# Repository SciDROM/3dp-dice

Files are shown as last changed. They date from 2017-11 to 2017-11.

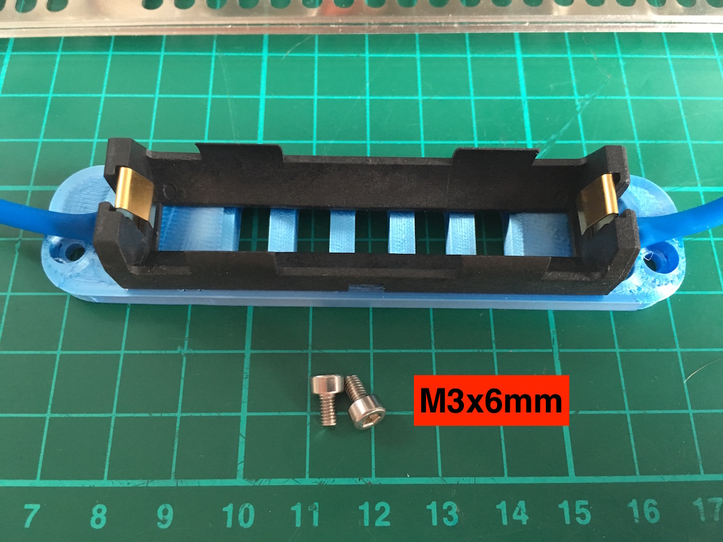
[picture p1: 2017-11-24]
optional/PiUSV+/parts.jpg

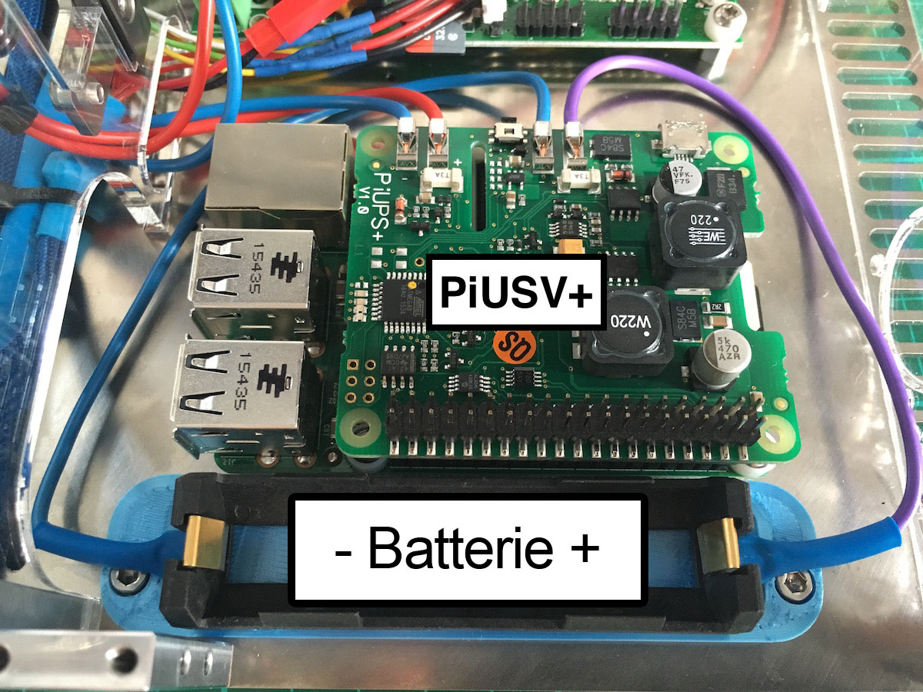
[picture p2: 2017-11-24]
optional/PiUSV+/whole_assembly.jpg

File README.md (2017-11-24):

# 3dp-dice

From https://well-engineered.net/index.php/en/projects/35-build-your-own-dice

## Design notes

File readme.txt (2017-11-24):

========================================

========================================

GERMAN:

30. April 2016 - Der Inhalt wird derzeit noch erstellt und komplettiert. Bei Fertigstellung wird dieses Dokument angepasst.

========

In diesem Ordner befinden sich alle benötigten Quelldateien für den Bau des 3D-Druckers „DICE“.

Die Benutzung ist unter folgenden Bedingungen erlaubt: Namensnennung - Nicht-kommerziell - Weitergabe unter gleichen Bedingungen 
CC BY-NC-SA

Diese Lizenz erlaubt es anderen, das Werk zu verbreiten, zu remixen, zu verbessern und darauf aufzubauen, allerdings nur nicht-kommerziell und solange René Jurack als Urheber des Originals genannt wird und die auf seinem Werk basierenden neuen Werke unter denselben Bedingungen veröffentlicht werden.

Link zur BOM (bill of material): https://docs.google.com/spreadsheets/d/1rdxKzCCWACPqPtby6bYP5xPDgSupsl8gtncckqbfDJk/

========================================

========================================

ENGLISH:

30. April 2016 - Files are under construction and needed to make complete. If finished, this document is going to get updated.

========

In this folder are all needed files to build the „DICE“.

Use it under following license: CC BY-NC-SA

Link to BOM (bill of material): https://docs.google.com/spreadsheets/d/1rdxKzCCWACPqPtby6bYP5xPDgSupsl8gtncckqbfDJk/

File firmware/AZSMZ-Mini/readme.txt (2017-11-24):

Config:

As of 15th may 2016: config.txt verified.

Firmware is Smoothieware.

Provided config-file is for the AZSMZ-mini V2.1 and to use in the 3D-printer ‚DICE’. More information at www.well-engineered.net

Firmware:

- always-up-to-date smoothieware-firmware to get at (deep-link): https://github.com/Smoothieware/Smoothieware/tree/edge/FirmwareBin

- Firmware.bin in this dropbox-folder is from 10. May 2016 (in case you are lazy and don’t want to download the newest)

How to:

- download firmware.bin from link above and save on SD-card

- save config.txt from dropbox on SD-card, too

- put SD-card into AZSMZ-mini, power on and press the reset-button once.

- wait for firmware to get ready.

- done.

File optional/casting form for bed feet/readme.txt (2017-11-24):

Cast for casting the distance sleeves beneath the printed.

Castmaterial is silicon for molds. (preferred).

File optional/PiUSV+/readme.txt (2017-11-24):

Battery mount for battery holder.
Battery is used for PiUSV+

Holder: https://www.reichelt.de/Batteriehalter-fuer-sonstige-Zellen/HA-1X18650-SA/3/index.html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

Battery: https://www.reichelt.de/Industriezellen/SANYO-18650-PCB/3/index.html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

PiUSV+: https://www.reichelt.de/Weiteres-Zubehoer/RPI-USV-/3/index.html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

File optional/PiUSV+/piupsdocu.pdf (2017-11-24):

CW2. PiUSV+

# CW2. PiUPS+

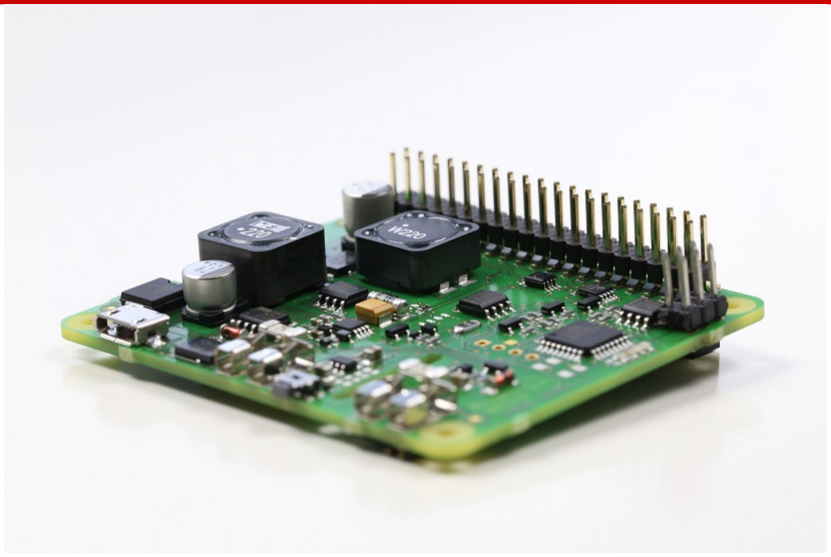
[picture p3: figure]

## Documentation CW2. PiUPS+

# Contents

I Introduction | 4
1 Function | 5
2 Technical information | 6
II Installation | 8
3 Hardware | 9
4 Software | 13

# List of Figures

2.1 Connecting assignment PiUPS+ | | 6
3.1 Start jumper configuration manually | | 9
3.2 Start jumper configuration automatically | | 9
3.3 Connecting the rechargeable battery | | 10
3.4 PiUPS+ on the Raspberry Pi with rechargeable battery | | 11
3.5 PiUPS+ with adapter | | 11
3.6 Alternative primary input | | 12

# Part I

# Introduction

# 1 Function

The PiUPS+ is an extension board for the Raspberry Pi. This extension can be used to ensure that the Pi is shut down in a safe manner in event of power failure. Corrupt and defective file systems on the SD card are therefor a thing of the past with this. In order to monitor the status of the PiUPS+ and be able to control it, the PiUPS-Monitorïs available that must be installed on the operating system of the Pi.

- Shutting down the Raspberry Pi in a safe manner
- Bridging longer power failures
- Switching off the Pi’s manually via the button on the PiUPS+

# 2 Technical information

Input primary voltage USB | +5VDC MicroUSB
Input primary voltage alternative | +5VDC bis +25VDC
Output current | up to 2,000mA¹
Output voltage | +5VDC +- 0.2V
Communication | I²C via address 0x30
Dimensions | L x W x H: 65 mm x 56.5 mm x 20 mm (corresponds with Raspberry Pi HAT specification)

## 2.1 CONNECTING DIAGRAM

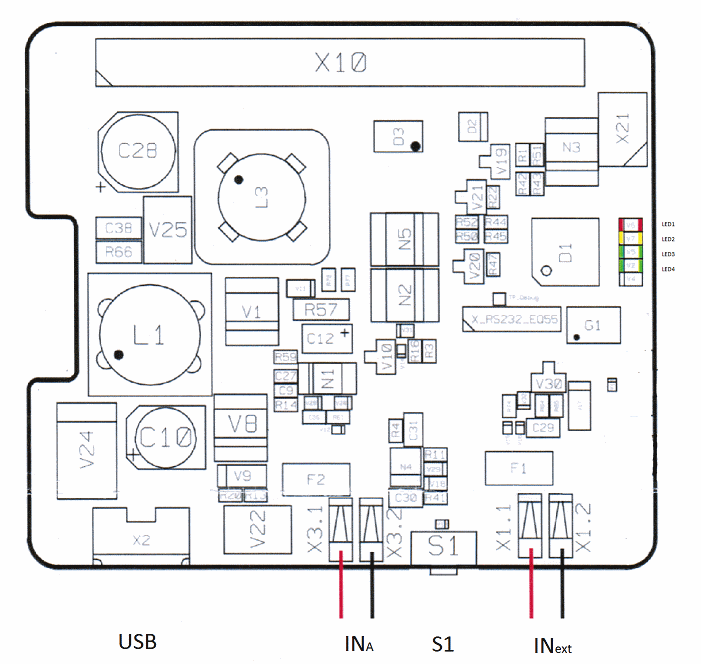
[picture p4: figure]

FIGURE 2.1: Connecting assignment PiUPS+

1depending on the power supply or rechargeable battery used

USB | MicroUSB-Buchse
INa | Connection of the rechargeable batteries (red = +, black = -)
INext | Alternative primary input. Permissible voltage +5VDC to +25VDC (red = +, black = -)
S1 | Switch for switching on / off (configuration via jumpers on the bottom)
LED1 (red) | LED illuminates: operation via both rechargeable battery, LED flashes: rechargeable battery not connected or is defective
LED2 (yellow) | Status display of the rechargeable battery. LED flashes: rechargeable battery charging, LED illuminates continuously: rechargeable battery charged
LED3 (green) | Status display PiUPS+. LED flashes: UPS operates correctly
LED4 (green) | Operation of the primary input

## 2.2 RECHARGEABLE BATTERY

The PiUPS+ can charge rechargeable batteries with the following specifications using the connection of the INa (Figure 2.1).Other rechargeable batteries / batteries must not be used under any circumstances.²

Technology | Lithium Ion (Li-Ion) or Lithium Polymer (LiPo)
Cells | 1
Capacity | min. 300mAh
Voltage | +3.7V
Discharge current | min. 3A
Charge voltage | +4.2V
Charge current | 100mA

2CW2. accepts no liability for damage caused by using other rechargeable batteries / batteries.

# Part II

# Installation

# 3 Hardware

Before commissioning the PiUPS+, you have to connect the rechargeable battery and configure the button as desired. We shall describe the precise process to you in the following steps.

## 3.1 SETTING THE BUTTON

The behaviour of the button of the PiUPS+ can be set using a jumper on the bottom of the PiUPS+. If you want to start the Pi manually via the button, you must insert the jumper in such a manner that it bridges both contacts.

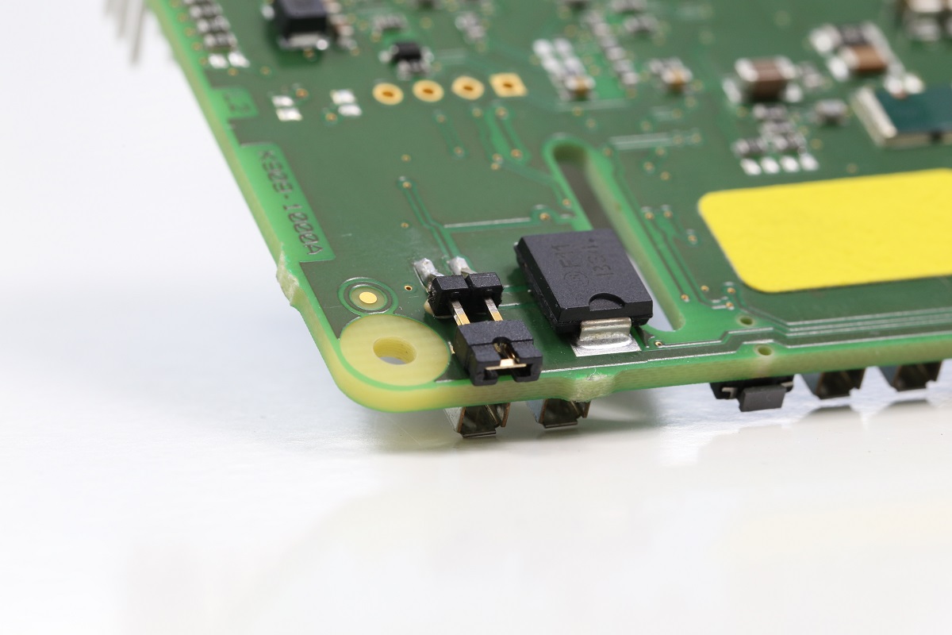
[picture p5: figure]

FIGURE 3.1: Start jumper configuration manually

If the Pi should be started automatically as soon as voltage is available at one of the primary inputs, insert the jumper so that the contacts are not connected.

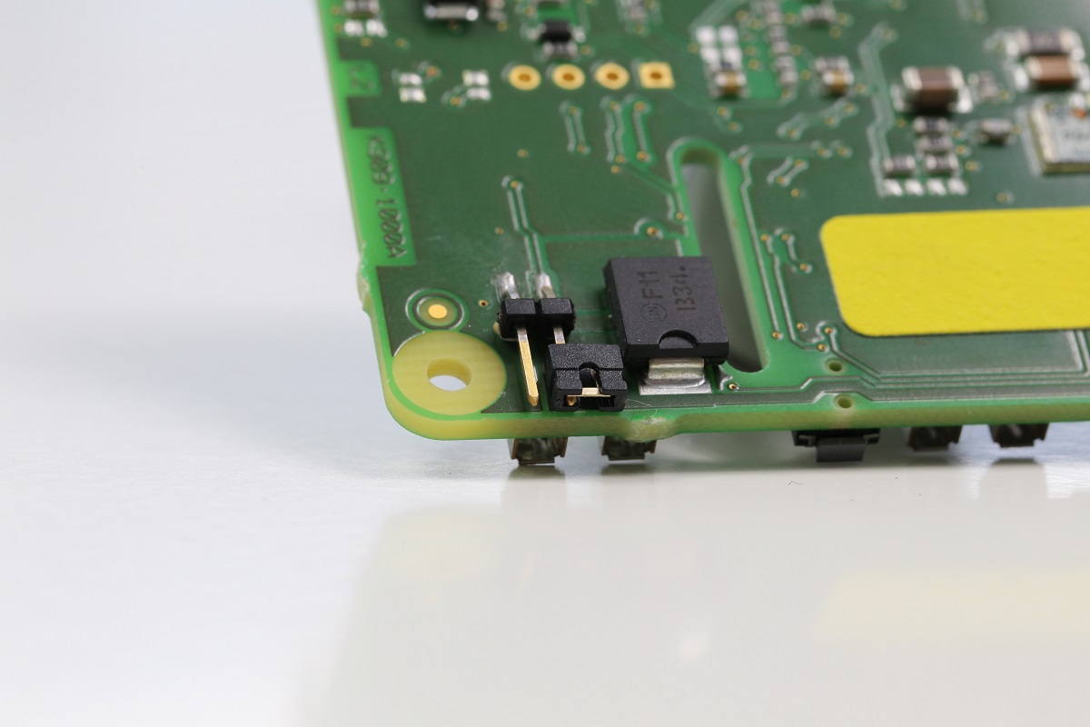
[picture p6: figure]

FIGURE 3.2: Start jumper configuration automatically

## 3.2 CONNECTING THE RECHARGEABLE BATTERY

ATTENTION! Please only use rechargeable batteries on this connection that have the specifications mentioned above. Other rechargeable batteries or batteries may lead to damaging the UPS and the Raspberry Pi!

Before you mount the PiUPS+ on the Pi, we recommend that you connect the rechargeable battery to the PiUPS+. In doing so, take care not to reverse the poles of the contacts for the rechargeable battery.
Generally, the rechargeable battery has a red braid and a black braid. Now please connect the connections of the rechargeable battery to the PiSUV+ as shown in the following figure.

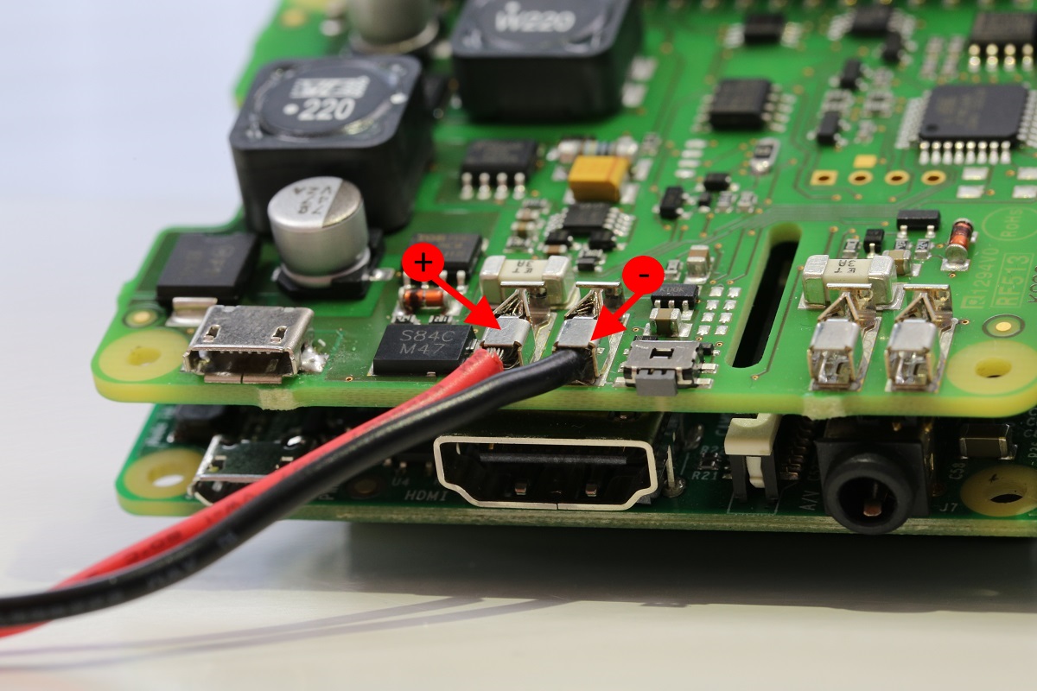
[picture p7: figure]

FIGURE 3.3: Connecting the rechargeable battery

## 3.3 INSTALLATION OF THE PIUPS+ ONTO THE RASPBER-

## RYPI

Now you can attach the PiUPS+ onto the RaspberryPi. Please note that in doing so, the pins of the GPIO ports cannot be inserted offset and the UPS cannot be attached to the Raspberry the wrong way around. This could lead to the destruction of the Pis and the PiUPS+.

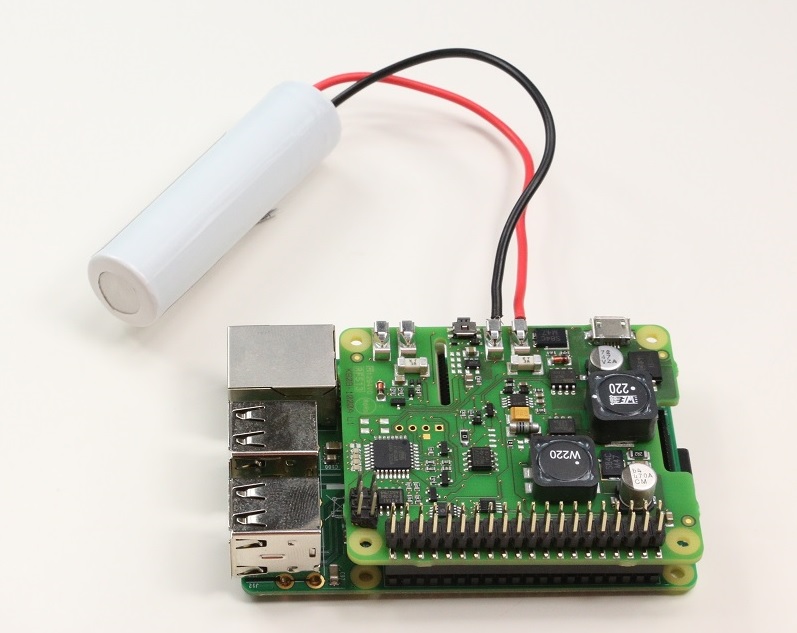
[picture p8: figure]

FIGURE 3.4: PiUPS+ on the Raspberry Pi with rechargeable battery

### 3.3.1 RASPBERRY PI MODEL A AND B

In order to be able to use the PiUPS+ wit Raspberry Pi model A or B, you need an adapter. Attach the adapter to the GPIO port of the Raspberry and ten the hPiUPS+ to the adapter as you can see in figure 3.5.

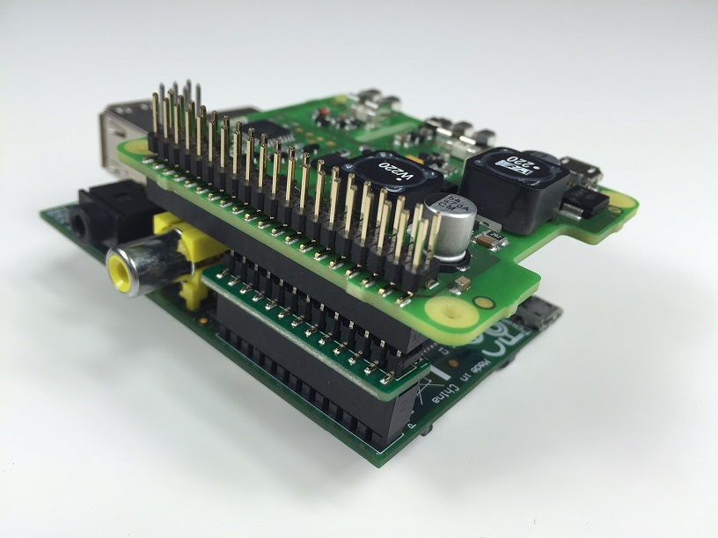
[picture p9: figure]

FIGURE 3.5: PiUPS+ with adapter

## 3.4 CONNECTING THE PRIMARY VOLTAGE

In order to be able to start the system, now you have to connect the primary voltage to the PiUPS+. Please do not use any USB power pack or active USB hubs on the Raspberry Pi. These may influence the function of the PiUPS+ so that switching off the system in a safe manner in event of power failure is not guaranteed.

### 3.4.1 USB

You can use the USB port on the PiUPS+ to supply the system with voltage. Depending on the configuration of the button, the system starts automatically or after you have pressed the button.

### 3.4.2 ALTERNATIVE INPUT

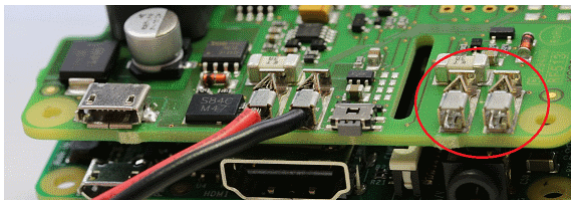
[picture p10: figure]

FIGURE 3.6: Alternative primary input

You can connect a voltage source with +5V to +25V to the alternative input. Please take note of the correct polarity when connecting (Figure 2.1)! These voltage sources are used instead of the USB port. The input is also monitored in the same manner as the USB port and in event of a power failure, the PiUPS+ automatically switches to the rechargeable battery connected in all cases.

# 4 Software

## 4.1 CONFIGURATION

You can influence the behaviour of the PiUPS monitor via the configuration. You have the following parameters at your disposal:

ShutdownTimer=<Time in seconds>
This value specifies how long the system continues to run after the voltage supply has switched to the rechargeable battery. Values between 1 - 999.999.999. are possible.

PowerOffTimer=<Time in seconds>
This value specifies how long the PiUPS+ should still stay switched on after the commend to shut down has been sent. A value between 1 - 255 can be entered here.

ShutdownCmd=<Command line>
This option is used to specify a command that should be used to shut down the Pi-UPS+. Here, e.g., you can enter the command for switching off or store your own script . If you store your own script, take care that the operating system is shut down by the script.

LogLevel=<notice|error|debug>
With this option, you can control which entries should be stored in the log.

LogStatusDesc=<0|1>
This command is used to influence if only a numeric value is logged for this value when changing the status, or a description as well.

## 4.2 RASPBIAN

Please download the current version of the des PiUPS monitor for the PiUPS+ from the support screen:
http://piups.net/support/

### 4.2.1 PREPARING FOR INSTALLATION

In order to allow the PiUPS monitor to operate correctly, the I²C-Bus must be activated first. Good instructions can be found the following screen: https://learn.adafruit.com/adafruits-raspberry-pi-lesson-4-gpio-setup/configuring-i2c

### 4.2.2 INSTALLATION

In order to be able to install the package under Raspbian, you must execute the following command in the directory with the package downloaded.

1 | sudo dpgk - i piupsmon - 0 . 8 . deb

### 4.2.3 USEAGE

When the PiUPS monitor is installed, you have the following commands available for starting and stopping the monitor:

1 | sudo / etc / i n i t . d/piupsmon s t a r t
1 | sudo / etc / i n i t . d/piupsmon stop
1 | sudo / etc / i n i t . d/piupsmon s ta t u s
| You can adapt the configuration in the following file: /etc/piupsmon/piupsmon.conf Do not forget to restart the PiUPS monitor after making an adjustment!
| The PiUPS monitor also saves a log in the following file: /var/log/piupsmon.log

## 4.3 MORE DISTRIBUTIONS

| We will be releasing packages for further distributions within the next few weeks. We shall also make the source text of the PiUPS monitor available online within the next few days.

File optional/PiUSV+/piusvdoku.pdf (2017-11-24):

CW2. PiUSV+

# CW2. PiUSV+


## Dokumentation CW2. PiUSV+

# Inhaltsverzeichnis

I Einführung | 4
1 Funktion | 5
2 Technische Informationen | 6
II Installation | 8
3 Hardware | 9
4 Software | 13

# Abbildungsverzeichnis

2.1 Anschlussbelegung PiUSV+ | | 6
3.1 Jumperkonfiguration manueller Start | | 9
3.2 Jumperkonfiguration automatischer Start | | 9
3.3 Anschluss Akku | | 10
3.4 PiUSV+ auf Raspberry Pi mit Akku | | 11
3.5 PiUSV+ mit Adapter | | 11
3.6 Alternativer Primäreingang | | 12

# Teil I

# Einführung

# 1 Funktion

Die PiUSV+ ist eine Erweiterungsplatine für den Rapberry Pi. Mit dieser Erweiterung können Sie sicherstellen, dass der Pi im Falle eines Stromausfalles sicher heruntergefahren wird. Korrupte und defekte Dateisysteme auf der SD-Karte gehören damit der Vergangenheit an. Um den Status der PiUSV+ überwachen und zu steuern zu können, gibt es den ”PiUSV-Monitor”, der auf dem Betriebssystem des Pi installiert werden muss.

- Sicheres Herunterfahren des Raspberry Pi
- Überbrückung von längeren Stromausfällen
- Manuelles Ausschalten des Pi’s über Taster an PiUSV+

# 2 Technische Informationen

Eingang Primärspannung USB | +5VDC MikroUSB
Eingang Primärspannung Alternativ | +5VDC bis +25VDC
Ausgangsstrom | bis zu 2000mA¹
Ausgangsspannung | +5VDC +- 0.2V
Kommunikation | per I²C über Adresse 0x30
Abmessungen | L x B H: 65 mm x 56,5 mm x 20 mm (entspricht Raspberry Pi HAT Vorgaben)

## 2.1 ANSCHLUSSPLAN


Abbildung 2.1: Anschlussbelegung PiUSV+

1Abhängig vom verwendeten Netzteil und Akku

USB | MikroUSB-Buchse
INa | Anschluss des Akkus (rot = +, schawarz = -)
INext | Alternativer Primäreingang. Zulässige Spannung +5VDC bis +25VDC (rot = +, schwarz = -)
S1 | Schalter zum Ein-/Ausschalten (Konfiguration über Jumper auf Unterseite)
LED1 (Rot) | Betrieb über Akku
LED2 (Gelb) | Status Anzeige des Akkus. LED Blinkt: Akku wird geladen, LED leuchtet dauerhaft: Akku ist voll
LED3 (Grün) | Status Anzeige PiUSV+. LED Blinkt: USV funktioniert ordnungsgemäß
LED4 (Grün) | Betrieb über Primäreingang

## 2.2 AKKU

Die PiUSV+ kann Akkus mit den folgenden Spezifikationen am Anschluss INa (Abbildung
2.1) aufladen. Es dürfen auf keinen Fall andere Akkus/Batterien verwendet werden.²
Technologie | Lithium Ionen (LiIon) oder Lithium Polymer (LiPo)
Zellen | 1
Kapazität | min. 300mAh
Spannung | +3.7V
Entladestrom | min. 3A
Ladespannung | +4.2V
Ladestrom | 100mA

2Für Schäden die durch die Verwendung von anderen Akkus oder Batterien entstehen übernimmt CW2.

keinerlei Haftung.

# Teil II

# Installation

# 3 Hardware

Vor der Inbetriebnahme der PiUSV+ müssen Sie den Akku anschließen und den Taster wie gewünscht konfigurieren. Den genauen Ablauf werden wir Ihnen in den nächsten Schritten erklären.

## 3.1 EINSTELLUNG TASTER

Das Verhalten des Tasters der PiUSV+ können Sie mit einem Jumper auf der Unterseite der PiUSV+ einstellen. Wenn Sie den Pi über den Taster manuell starten wollen, müssen Sie den Jumper so aufstecken, dass dieser die beiden Kontakte überbrückt.


Abbildung 3.1: Jumperkonfiguration manueller Start

Soll der Pi automatisch starten sobald die Spannung an einem der primären Eingänge anliegt, stecken Sie den Jumper so auf, dass die Kontakte nicht verbunden sind.


Abbildung 3.2: Jumperkonfiguration automatischer Start

## 3.2 ANSCHLUSS AKKU

ACHTUNG! Bitte verwenden Sie an diesem Anschluss nur Akkus mit den oben genannten Spezifikationen! Andere Akkus oder Batterien können zur Beschädigung der USV und des Raspberry Pi führen!

Bevor sie die PiUSV+ auf dem Pi montieren, empfehlen wir Ihnen den Akku an der PiUSV+ anzuschließen. Es ist dabei unbedingt darauf zu achten, dass die Kontakte des Akkus nicht verpolt werden.
In der Regel haben Sie am Akku eine rote Litze und eine schwarze Litze. Die Anschlüsse des Akkus schließen Sie nun bitte wie auf der folgenden Grafik gezeigt an der PiUSV+ an.


Abbildung 3.3: Anschluss Akku

## 3.3 INSTALLATION DER PIUSV+ AUF DEM RASPBERRYPI

Die PiUSV+ können Sie nun auf derm RaspberryPi aufstecken. Bitte beachten Sie dabei, dass die Pins der GPIO-Ports nicht versetzt gesteckt werden und die USV nicht verkehrtherum auf dem Raspberry aufgesetzt wird. Dies kann zur Zerstörung der Pis und der PiUSV+ führen.


Abbildung 3.4: PiUSV+ auf Raspberry Pi mit Akku

### 3.3.1 RASPBERRY PI MODELL A UND B

Um die PiUSV+ mit dem Raspberry Pi Modell A oder B verwenden zu können, benötigen Sie einen Adapter. Den Adapter stecken Sie auf die GPIO-Ports des Raspberry und die PiUSV+ anschließend auf den Adapter wie in Abbildung 3.5 zu erkennen.


Abbildung 3.5: PiUSV+ mit Adapter

## 3.4 ANSCHLUSS PRIMÄRSPANNUNG

Um das System nun starten zu können, müssen Sie noch die Primärspannung an der Pi-USV+ anschließen. Bitte verwenden Sie am Raspberry Pi kein USB-Netzteil, oder aktive USB Hubs. Diese können die Funktion der PiUSV+ beeinträchtigen, so dass kein sicheres Ausschalten des Systems bei einem Strommausfall gewährleistet ist.

### 3.4.1 USB

Sie können den USB-Eingang auf der PiUSV+ verwenden, um das System mit Spannung zu versorgen. Je nach Konfiguration des Tasters startet das System nun automatisch oder nachdem Sie auf den Schalter gedrückt haben.

### 3.4.2 ALTERNATIVER EINGANG


Abbildung 3.6: Alternativer Primäreingang

Am alternativen Eingang können Sie eine Spannungsquelle mit +5V bis +25V anschließen. Bitte achten Sie auf die korrekte Polung beim Anschließen (Abbildung 2.1)! Diese Spannungsquelle wird anstelle des USB-Eingangs verwendet. Der Eingang wird ebenfalls wie der USB-Eingang überwacht und die PiUSV+ schaltet im Falle des Stromausfalls automatisch auf den angeschlossenen Akku.

# 4 Software

## 4.1 KONFIGURATION

Sie können das Verhalten der PiUSV-Monitors über die Konfiguration beeinflussen. Ihnen stehen dazu folgende Parameter zur Verfügung:

ShutdownTimer=<Zeit in Sekunden>
Dieser Wert gibt an, wie lange das System weiter läuft, nachdem die Spannungsversorgung auf den Akku gewechselt ist. Es sind Werte zwischen 1 - 999.999.999. möglich.

PowerOffTimer=<Zeit in Sekunden>
Dieser Wert gibt an, wie lange die PiUSV+ noch eingeschaltet bleiben soll, nachdem der Befehl zum Herunterfahren gesendet wurde. Es kann hier ein Wert zwischen 1 -255 angegeben werden.

ShutdownCmd=<Befehlszeile>
Mit dieser Option geben Sie einen Befehl an, mit dem die PiUSV+ heruntergefahren werden soll. Sie können hier z.B. direkt den Befehl zum Ausschalten geben oder ein eigenes Skript hinterlegen. Wenn Sie ein eigenes Skript hinterlegen, müssen Sie darauf achten, dass das Betriebssystem durch das Skript heruntergefahren wird.

LogLevel=<notice|error|debug>
Mit dieser Option können Sie steuern, welche Einträge im Log gespeichert werden sollen.

LogStatusDesc=<0|1>
Mit dem Befehl können Sie beinflussen, ob bei Statusänderungen nur ein nummerischer Wert oder auch eine Beschreibung zu diesem Wert geloggt wird.

## 4.2 RASPBIAN

Bitte laden Sie sich die aktuellste Version des PiUSV-Monitors für die PiUSV+ auf der Support-Seite herunter:
http://piusv.de/support/

### 4.2.1 VORBEREITUNG INSTALLATION

Damit der PiUSV-Monitor ordnungsgemäß funktioniert, müssen Sie zuerst den I²C-Bus aktivieren.
Eine gute Anleitung dazu finden Sie auf der folgenden Seite: https://learn.adafruit.com/adafruits-raspberry-pi-lesson-4-gpio-setup/configuring-i2c

### 4.2.2 INSTALLATION

Um das Paket unter Raspbian zu installieren, müssen Sie folgenden Befehl im Verzeichnis mit dem heruntergeladenen Paket ausführen:

1 | sudo dpgk - i piupsmon - 0 . 8 . deb

### 4.2.3 VERWENDUNG

| Wenn der PiUSV-Monitor installiert ist, stehen Ihnen folgende Befehle zum Starten und Stop- pen des Monitors zur Verfügung:
1 | sudo / etc / i n i t . d/piupsmon s t a r t
1 | sudo / etc / i n i t . d/piupsmon stop
1 | sudo / etc / i n i t . d/piupsmon s ta t u s
| Die Konfiguration können Sie in der folgenden Datei anpassen: /etc/piupsmon/piupsmon.conf Vergessen Sie nach einer Anpassung bitte nicht den PiUSV-Monitor neuzustarten!
| Der PiUSV-Monior legt auch ein Log in folgender Datei an: /var/log/piupsmon.log

## 4.3 WEITERE DISTRIBUTIONEN

| Wir werden in den nächsten Wochen noch Pakete für weitere Distributionen veröffentlichen. Den Quelltext des PiUSV-Monitors werden wir ebenfalls in den nächsten Tagen online zur Verfügung stellen.

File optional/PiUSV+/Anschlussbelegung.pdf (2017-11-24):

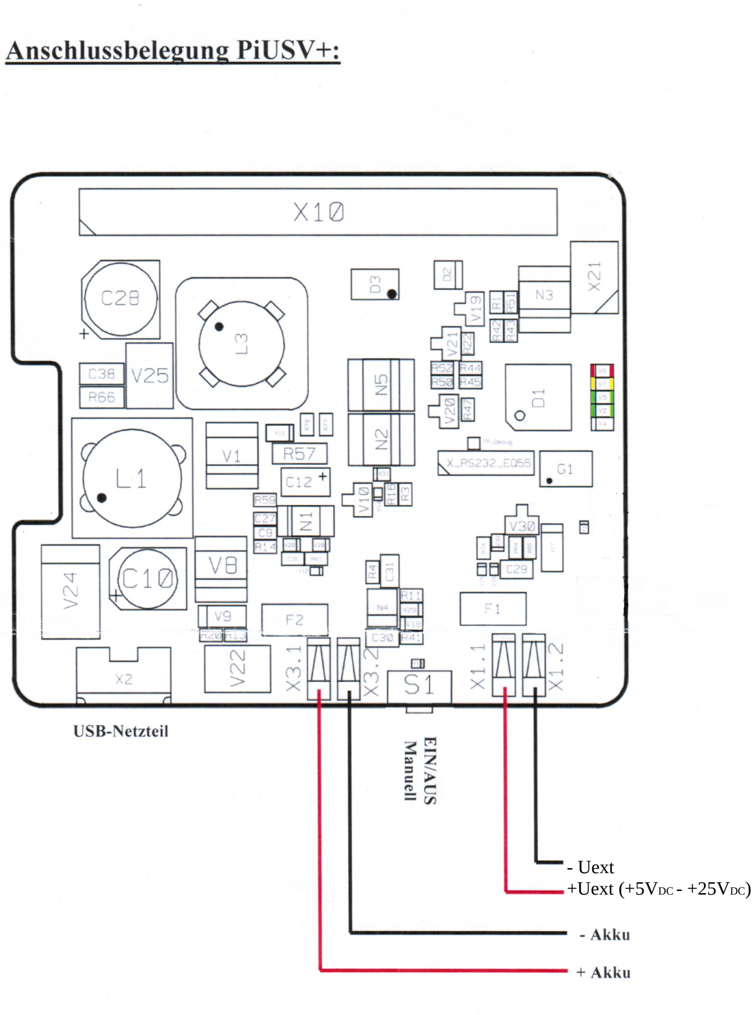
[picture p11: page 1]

- Uext
+Uext (+5VDC - +25VDC)

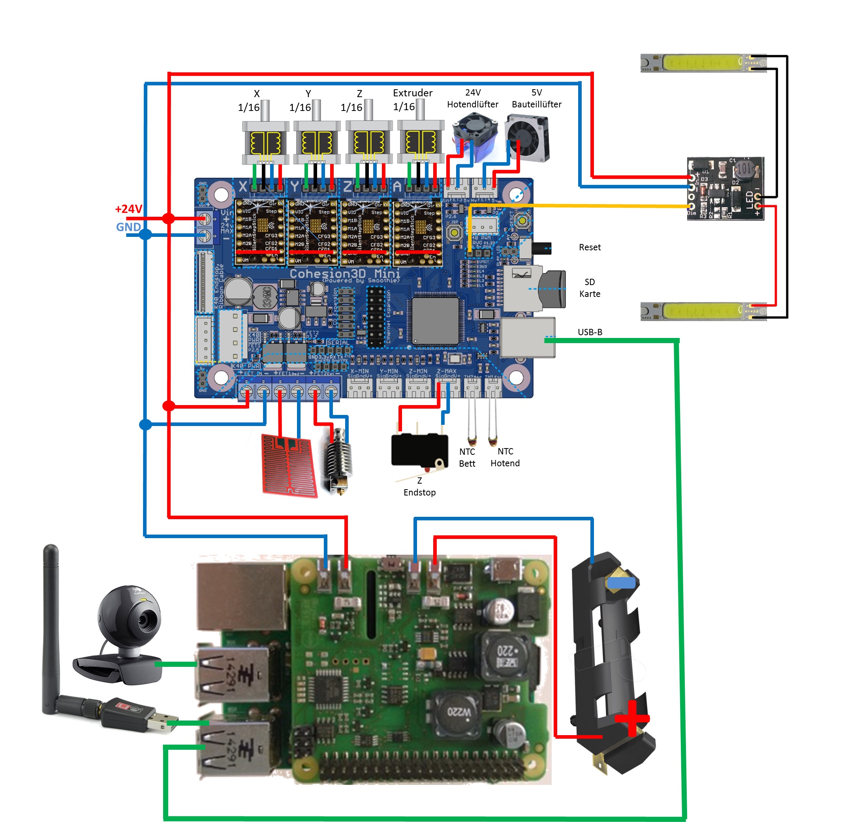
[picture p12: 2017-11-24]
electric/Dice Schematic.jpg

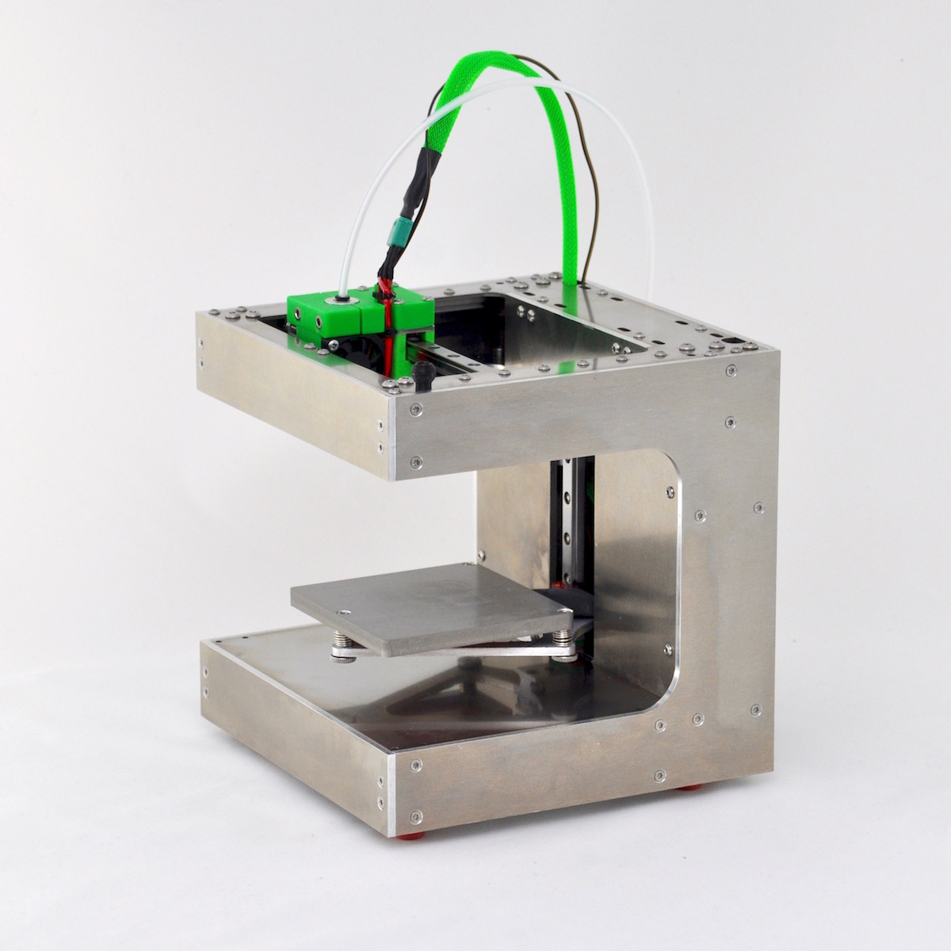
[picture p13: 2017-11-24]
dice.jpg

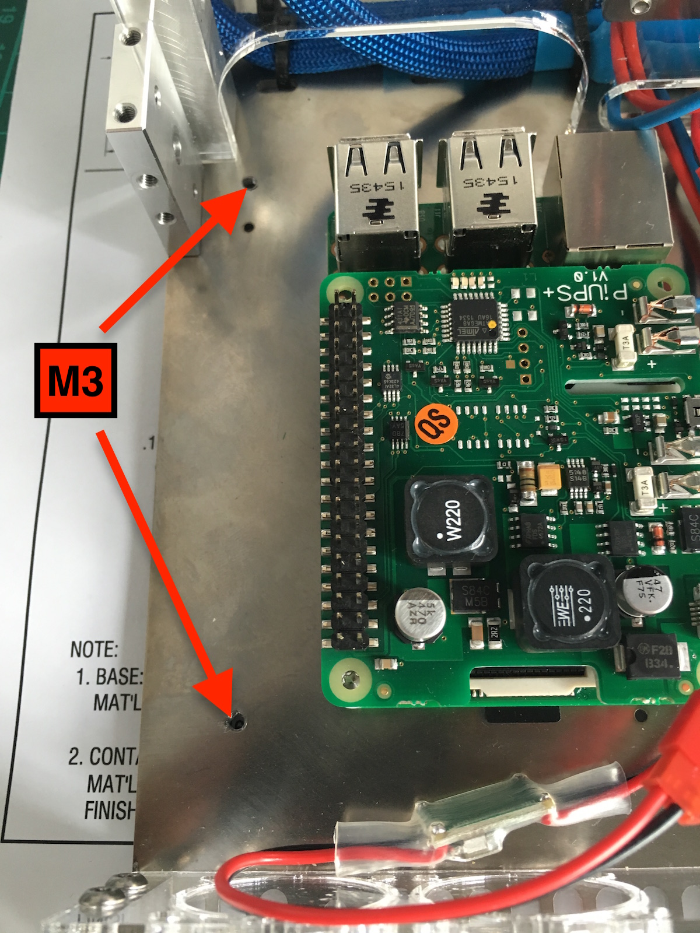
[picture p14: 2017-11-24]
optional/PiUSV+/tap_M3.jpg

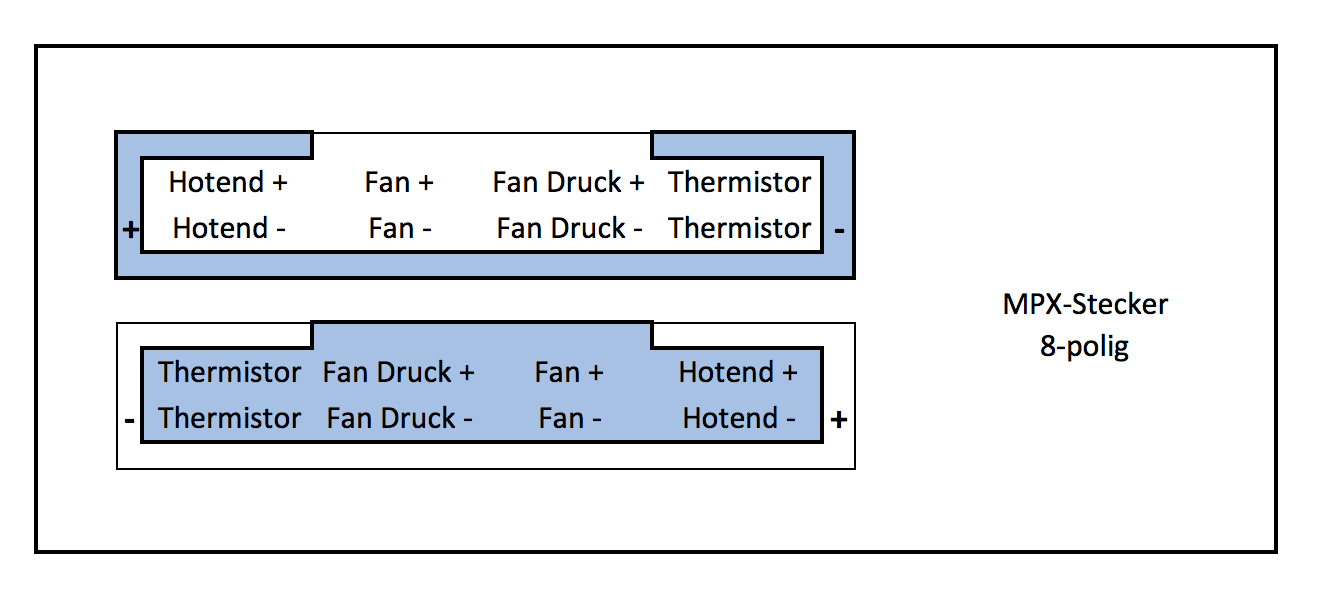
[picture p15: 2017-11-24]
electric/pin-assignment - connector hotend.png

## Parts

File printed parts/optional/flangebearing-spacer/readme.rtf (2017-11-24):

========================================
========================================

GERMAN:

========

2 Versionen der Spacer mit 4mm und 4,5mm Innendurchmesser. Je nachdem, wie euer Drucker kalibriert ist, ist es vielleicht nötig, mit einem größeren Innendurchmesser zu drucken.

Namensnennung:

Spacer 0.4mm .scad und .stl Datei von:
reprap.org Forum-user 'bastard'

========================================
========================================

ENGLISH:

========

2 versions of the spacer with 4mm or 4,5mm inner diameter. Depending on how you calibrated your printer, it is maybe useful to print with a bigger inner diameter.

Credits:
Spacer 0.4mm .scad and .stl files from:
reprap.org Forum-user 'bastard'

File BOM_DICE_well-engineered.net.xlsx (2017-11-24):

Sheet: deutsch BOM
letzte Änderung: |  | 30.09.2017 - Rene Jurack |  | BOM IST FERTIG!
Alle Infos auf: well-engineered.net - bau dir deinen eigenen DICE (http://well-engineered.net/index.php/de/projekte/32-bau-dir-deinen-eigenen-dice) |  |  |  | Der Onlineshop youprintin3d.de kooperiert mit well-engineered.net und stellt einen Großteil der benötigten Komponenten in seinem Sortiment zur Verfügung. Eine gute Gelegenheit, Porto zu sparen!
BOM - DICE
Position | Menge | Einheit | Bezeichnung | Material / Typ | Links |  |  | Zeichnung | Lieferant | Einzelpreis | Porto | Gesamtpreis | Bemerkung
 |  |  |  |  | ebay.de | ebay.us | andere
 | Mechanik
1 | 1 | Set | Laserbleche | Aluminiumblech 4mm, einseitig foliert | - |  |  | DXF | well-engineered.net | 148.67 € |  | 148.67 € | 7 Teile
 |  |  |  | Edelstahlblech 2mm, einseitig foliert |  |  |  |  |  |  |  |  | 12 Teile
2 | 1 | Set | Frästeile | Aluminium, eloxiert | - |  |  | DXF | well-engineered.net | 121.41 € |  | 121.41 €
3 | 1 | Stk | Extruder | E3D-Titan | - |  |  |  | youprintin3d.de | 70.00 € |  | 70.00 €
4 | 1 | Stk | Druckplatte | feinstgefräst, 5mm Alu | goo.gl/06ZiHY |  |  | DXF | youprintin3d.de | 7.00 € |  | 7.00 € | Bei der Bestellung Kommentar hinzufügen: "Für DICE"
5 | 3 | Stk | Druckfedern | 0,8 x 10 x 15 mm | http://goo.gl/QoOyr6 | - |  | nein | ebay | 0.20 € |  | 0.60 €
6 | 24 | Stk | Flanschkugellager | MF104ZZ | http://goo.gl/NbtYXf | http://goo.gl/2QXC5a | https://goo.gl/RH7Nfo | nein | youprintin3d.de | 1.20 € |  | 28.80 €
7 | 2 | Stk | Pulley | GT2 | http://goo.gl/qit420 | http://goo.gl/iHjEF0 | https://goo.gl/eRgcD4 | nein | youprintin3d.de | 5.00 € |  | 10.00 €
8 | 2 | Meter | Riemen | GT2 | http://goo.gl/IbiPAF | http://goo.gl/I6Z5PW | https://goo.gl/AfOT92 | nein | youprintin3d.de | 5.00 € |  | 10.00 €
9 | 1 | Meter | Luftschlauch | 4x6 | http://goo.gl/kTljEC | http://goo.gl/4pU3a1 |  | nein | ebay
10 | 2 | Stk | Linearschienen + Wagen | Misumi SSEBL10-140-MC | https://goo.gl/NhqKSm |  |  | nein | youprintin3d.de | 169.99 € |  | 169.99 € | 120mm
11 | 2 | Stk | Linearschienen + Wagen | Misumi SSEBL10-120-MC |  |  |  |  |  |  |  |  | 140mm
12 | 1 | Stk | Druckplatte | mtPlus |  |  |  |  | well-engineered.net | 18.00 € |  | 18.00 €
13 | 1 | Set | Druckteile | PETG |  |  |  |  | well-engineered.net | 25.00 € |  | 25.00 €
 | Motoren
14 | 3 | Stk | NEMA 17 | 17HS4417 | http://goo.gl/zx7cDu | http://goo.gl/sFZ0Jc | https://goo.gl/UsYIfO | nein | youprintin3d.de | 15.00 € |  | 45.00 € | max 40mm Motorlänge
15 | 1 | Stk | NEMA 17 mit TR8x4 (P2) Spindel | 42HS34-1334 | http://goo.gl/obI88D | http://goo.gl/obI88D |  | nein | Aliexpress | 30.00 € |  | 30.00 € | max 34mm Motorlänge, Spindellänge min.150mm
 | Elektrik
16 | 1 | Stk | Hotend | E3D-V6, Bowden | youprintin3d.de | youprintin3d.de | https://goo.gl/k831Pu | nein | youprintin3d.de | 85.00 € |  | 85.00 €
17 | 1 | Stk | Radiallüfter 35mm | 3510 | N/A | N/A |  | nein | well-engineered.net | 15.00 € |  | 15.00 €
18 | 2 | Stk | Lüfter | 30x6mm, 5V | http://goo.gl/mm9Bis | http://goo.gl/tRvZrV |  | nein | ebay | 6.10 € |  | 12.20 € | (5 cfm / MC30060V1-000U-A99) The number after the V is the speed of the fan: V3->slow; V2-> medium; V1->fast; VX-> very fast.
19 | 1 | Stk | Tischnetzteil | 24V 5A 120W | http://goo.gl/srKHM9 | http://goo.gl/9DQIgl | http://amzn.to/2mP7d9e | nein | amazon | 36.00 € |  | 36.00 €
20 | 1 | Stk | Heizmatte | 24V / 60W / 90x90mm | - | - |  | nein | well-engineered.net | 18.75 € |  | 18.75 €
21 | 1 | Stk | Controllerboard | Cohesion3d Mini | cohesion3d.com |  |  | nein | well-engineered.net | 85.00 € |  | 85.00 €
22 | 4 | Stk | Schrittmotortreiber | TMC2100 | watterott.com |  |  | nein | watterott.de | 12.00 € |  | 48.00 €
23 | 1 | Set | Wärmeleitklebefolie |  | http://goo.gl/JmxsbC | http://goo.gl/mDuREi |  | nein | ebay | 8.00 € |  | 8.00 €
24 | 1 | Set | MPX Stecker/Buchse Set 8 polig |  | http://goo.gl/i2l7PM | http://goo.gl/i2l7PM |  | nein | höllein-shop | 2.30 € |  | 2.30 €
25 | 1 | Stk | Microswitch | Endschalter Z | http://goo.gl/YcjI51 | N/A | klick (https://youprintin3d.de/hardware/endstops/444/endstop-microswitches-omron-d2f-01fl.html?sPartner=renejurack) | nein | youprintin3d.de | 2.49 € |  | 2.49 €
26 | 2 | Meter | Kabel | LIYY 4x0,14 |  |  |  | nein | ebay | 3.00 € |  | 6.00 €
27 | 2 | Stk | Micro SD Karte |  | http://goo.gl/PgGwky |  |  | nein | amazon | 9.00 € |  | 18.00 €
28 | 1 | Stk | Raspberry Pi 3 |  | http://goo.gl/0EhuRW |  |  | nein | amazon | 38.00 € |  | 38.00 €
29 | 1 | Stk | USB-Kabel 20cm |  | http://goo.gl/CbHR9c | http://goo.gl/wiRoCx |  | nein | ebay/amazon | 5.00 € |  | 5.00 €
 | Schrauben und dergleichen
 | Ein komplettes Set aller hier aufgelisteten und grün markierten Schrauben und Muttern (Schraubenkit) erhaltet ihr als Paket bei youprintin3d.de |  |  |  | https://goo.gl/TUIFZH |  |  | nein | youprintin3d.de | 19.00 € |  | 19.00 €
30 | 26 | Stk | Linsenkopfschraube Torx | M3 x 6mm |  |  |  | nein | youprintin3d.de
31 | 22 | Stk | Linsenkopfschraube Torx | M3 x 8mm |  |  |  | nein | youprintin3d.de
32 | 6 | Stk | Linsenkopfschraube Torx | M3 x 12mm |  |  |  | nein | youprintin3d.de
33 | 4 | Stk | Linsenkopfschraube Torx | M3 x 40mm |  |  |  | nein | youprintin3d.de
34 | 19 | Stk | Linsenkopfschraube Torx | M4 x 6mm |  |  |  | nein | youprintin3d.de
35 | 8 | Stk | Linsenkopfschraube Torx | M4 x 10mm |  |  |  | nein | youprintin3d.de
36 | 8 | Stk | Linsenkopfschraube Torx | M4 x 40mm |  |  |  | nein | youprintin3d.de
37 | 22 | Stk | Inbus Zylinderkopf | M3 x 6mm |  |  |  | nein | youprintin3d.de
38 | 15 | Stk | Inbus Zylinderkopf | M3 x 16mm |  |  |  | nein | youprintin3d.de
39 | 4 | Stk | Inbus Zylinderkopf | M3 x 20mm |  |  |  | nein | youprintin3d.de
40 | 2 | Stk | Inbus Zylinderkopf | M3 x 50mm |  |  |  | nein | youprintin3d.de
41 | 2 | Stk | Inbus Zylinderkopf | M4 x 20mm |  |  |  | nein | youprintin3d.de
42 | 1 | Stk | Inbus Zylinderkopf | M5 x 16mm |  |  |  | nein | youprintin3d.de
43 | 12 | Stk | Senkkopfschraube Torx | M3 x 5mm |  |  |  | nein | youprintin3d.de
44 | 66 | Stk | Senkkopfschraube Torx | M3 x 10mm |  |  |  | nein | youprintin3d.de
45 | 2 | Stk | Senkkopfschraube Torx | M4 x 25mmm (selber kürzen auf 23mm!) |  |  |  | nein | youprintin3d.de
46 | 2 | Stk | Schraube | M2x12mm |  |  |  | nein | youprintin3d.de
47 | 4 | Stk | HDD/PC-Schrauben | M3 x 6mm (ISO 7380) |  |  |  | nein | youprintin3d.de
48 | 8 | Stk | Abstandsbolzen | M3 x 5mm |  |  |  | nein | youprintin3d.de
49 | 16 | Stk | Unterlegscheibe | M3 |  |  |  | nein | youprintin3d.de
50 | 6 | Stk | Unterlegscheibe | M4 |  |  |  | nein | youprintin3d.de
51 | 8 | Stk | Sechskantmuttern DIN 439 | M4 flach | http://goo.gl/UCgb0k |  |  | nein | youprintin3d.de
52 | 12 | Stk | Mutter | M3 |  |  |  | nein | youprintin3d.de
53 | 1 | Stk | Mutter selbstsichernd | M3 |  |  |  | nein | youprintin3d.de
54 | 3 | Stk | Rändelmuttern | DIN 467 niedrige Form Edelstahl M3 | http://goo.gl/Mnz4qC | http://goo.gl/b58PFm |  | nein | youprintin3d.de
55 | 2 | Stk | Einpressmuttern | M4 |  |  |  | nein | aliexpress | 0.20 € |  | 0.20 €
56 | 100 | Stk | Kabelbinder | 3x1x100 |  |  |  | nein | ebay | 5.00 € |  | 7.00 €
57 | 1 | Set | Gewebeschlauch | 12mm innen |  |  |  | nein | ebay | 5.00 € |  | 5.00 €
 |  |  |  |  |  |  |  |  |  |  |  | 1095.41 €

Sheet: english BOM
last change: |  | 30.09.2017 - Rene Jurack |  | english BOM IS ready!
All infos to find at: well-engineered.net - build your own DICE (http://well-engineered.net/index.php/en/projects/35-build-your-own-dice) |  |  |  | The onlineshop youprintin3d.de cooperates with well-engineered.net and put up a big chunk of the needed parts. Quite a bargain to save on shipping-costs!
BOM - DICE
increment | amount | unit | name | material / type | links |  | schematic | seller | price / unit | shipping | total price | remarks
 |  |  |  |  | ebay.de | ebay.us
 | mechanical
1 | 1 | Set | lasered sheets | Aluminiumsheet 4mm, filmed on one side | - |  | DXF | well-engineered.net | 148.67 € |  | 148.67 € | 7 parts
 |  |  |  | stainless steel sheet 2mm, filmed on one side |  |  |  |  |  |  |  | 12 parts
2 | 1 | Set | milled parts | aluminium, eloxed | - |  | DXF | well-engineered.net | 121.41 € |  | 121.41 €
3 | 1 | pcs | Extruder | E3D-Titan |  |  |  | youprintin3d.de | 70.00 € |  | 70.00 €
4 | 1 | pcs | printbed | precision milled 5mm warmcasted Aluminium | - | - | DXF | youprintin3d.de | 7.00 € |  | 7.00 €
5 | 3 | pcs | compressing spring | 0,8 x 10 x 15 mm | http://goo.gl/QoOyr6 | - | no |  | 0.20 € |  | 0.60 €
6 | 24 | pcs | flange bearings | MF104ZZ | http://goo.gl/NbtYXf | http://goo.gl/2QXC5a | no | youprintin3d.de | 1.20 € |  | 28.80 €
7 | 2 | pcs | Pulley | GT2 | http://goo.gl/qit420 | http://goo.gl/iHjEF0 | no | youprintin3d.de | 5.00 € |  | 10.00 €
8 | 2 | meter | belt | GT2 | http://goo.gl/IbiPAF | http://goo.gl/I6Z5PW | no | youprintin3d.de | 5.00 € |  | 10.00 €
9 | 1 | meter | pneumatic tube | 4x6 | http://goo.gl/kTljEC | http://goo.gl/4pU3a1 | no
10 | 2 | pcs | linear rail + carriage | Misumi SSEBL10-140 | youprintin3d.de |  | no | youprintin3d.de | 169.99 € |  | 169.99 € | 120mm
11 | 2 | pcs | linear rail + carriage | Misumi SSEBL10-120 |  |  |  |  |  |  |  | 140mm
12 | 1 | pcs | printbed | mtPlus |  |  |  | well-engineered.net | 18.00 € |  | 18.00 €
13 | 1 | set | printed parts | PETG |  |  |  | well-engineered.net | 25.00 € |  | 25.00 €
 | motors
14 | 3 | pcs | NEMA 17 | 17HS4417 | http://goo.gl/zx7cDu | http://goo.gl/sFZ0Jc | no | youprintin3d.de | 15.00 € |  | 45.00 € | max 40mm Motorlänge
15 | 1 | pcs | NEMA 17 with TR8x4 (P2) spindle | 42HS34-1334 | http://goo.gl/obI88D | http://goo.gl/obI88D | no | Aliexpress | 30.00 € |  | 30.00 € | max 34mm Motorlänge, Spindellänge min.150mm
 | electrical parts
16 | 1 | pcs | Hotend | E3D-V6, Bowden | youprintin3d.de | youprintin3d.de | no | youprintin3d.de | 85.00 € |  | 85.00 €
17 | 1 | pcs | radial fan 35mm | 3510 | N/A | N/A | no | well-engineered.net | 15.00 € |  | 15.00 €
18 | 3 | pcs | fan | 30x6mm, 5V | http://goo.gl/mm9Bis | http://goo.gl/tRvZrV | no | ebay | 6.10 € |  | 12.20 € | (5 cfm / MC30060V1-000U-A99) The number after the V is the speed of the fan: V3->slow; V2-> medium; V1->fast; VX-> very fast.
19 | 1 | pcs | desktop charger | 24V 5A 120W | http://goo.gl/srKHM9 | http://goo.gl/9DQIgl | no | ebay | 36.00 € |  | 36.00 € | Maße: 133x58x33mm
20 | 1 | pcs | kapton heater for printbed | 24V / 60W / 90x90mm | - | - | no | well-engineered.net | 18.75 € |  | 18.75 €
21 | 1 | pcs | Controllerboard | Chohesion3d Mini | cohesion3d.com |  | no | well-engineered.net | 85.00 € |  | 85.00 €
22 | 4 | pcs | stepper drivers | TMC2100 | watterott.com |  | no | watterott.com | 12.00 € |  | 48.00 €
23 | 1 | Set | thermal adhesive pad |  | http://goo.gl/JmxsbC | http://goo.gl/mDuREi | no | ebay | 8.00 € |  | 8.00 €
24 | 1 | Set | MPX plug Set 8 pol |  | http://goo.gl/i2l7PM | http://goo.gl/i2l7PM | no | höllein-shop | 2.30 € |  | 2.30 €
25 | 1 | pcs | Microswitch | endstop Z | http://goo.gl/YcjI51 | N/A | no | youprintin3d.de | 2.49 € |  | 2.49 €
26 | 2 | Meter | Kabel | LIYY 4x0,14 |  |  | no | ebay | 3.00 € |  | 6.00 €
27 | 1 | pcs | Micro SD Karte |  |  |  | no |  | 9.00 € |  | 18.00 €
28 | 1 | pcs | Raspberry Pi 3 |  | http://goo.gl/0EhuRW |  | no | amazon | 38.00 € |  | 38.00 €
29 | 1 | pcs | USB-cable 20cm |  | http://goo.gl/CbHR9c | http://goo.gl/wiRoCx | no | ebay/amazon | 5.00 € |  | 5.00 €
 | screws and other hardwareparts
 | A complete set of all listed screws marked in green is available as a kit from youprintin3d.de |  |  |  | https://youprintin3d.de/3d-drucker/dice-der-edle-minidrucker/615/schraubenkit-dice-minidrucker.html |  | no | youprintin3d.de | 19.00 € |  | 19.00 €
30 | 26 | pcs | cheese-head screw torx | M3 x 6mm |  |  | no | youprintin3d.de
31 | 22 | pcs | cheese-head screw torx | M3 x 8mm |  |  | no | youprintin3d.de
32 | 6 | pcs | cheese-head screw torx | M3 x 12mm |  |  | no | youprintin3d.de
33 | 4 | pcs | cheese-head screw torx | M3 x 40mm |  |  | no | youprintin3d.de
34 | 19 | pcs | cheese-head screw torx | M4x6mm
35 | 8 | pcs | cheese-head screw torx | M4 x 10mm |  |  | no | youprintin3d.de
36 | 8 | pcs | cheese-head screw torx | M4 x 40mm |  |  | no | youprintin3d.de
37 | 22 | pcs | cylinderhead bolt inbus | M3 x 6mm |  |  | no | youprintin3d.de
38 | 15 | pcs | cylinderhead bolt inbus | M3 x 16mm |  |  | no | youprintin3d.de
39 | 4 | pcs | cylinderhead bolt inbus | M3 x 20mm |  |  | no | youprintin3d.de
40 | 2 | pcs | cylinderhead bolt inbus | M3 x 50mm |  |  | no | youprintin3d.de
41 | 2 | pcs | cylinderhead bolt inbus | M4 x 20mm |  |  | no | youprintin3d.de
42 | 1 | pcs | cylinderhead bolt inbus | M5 x 16mm |  |  | no | youprintin3d.de
43 | 12 | pcs | countersunk bolt DIN965 VA | M3 x 5mm |  |  | no | youprintin3d.de
44 | 66 | pcs | countersunk bolt DIN965 VA | M3 x 10mm |  |  | no | youprintin3d.de
45 | 2 | pcs | countersunk bolt DIN965 VA | M4 x 25mmm (shorten to 23mm!) |  |  | no | youprintin3d.de
46 | 2 | pcs | screw | M2x12mm |  |  | no | youprintin3d.de
47 | 4 | pcs | HDD/PC-screw | M3 x 6mm (ISO 7380) |  |  | no | youprintin3d.de
48 | 8 | pcs | standof-nut | M3 x 5mm |  |  | no | youprintin3d.de
49 | 16 | pcs | washer | M3 |  |  | no | youprintin3d.de
50 | 6 | pcs | washer | M4 |  |  | no | youprintin3d.de
51 | 8 | pcs | nut DIN 439 | M4 flat | http://goo.gl/UCgb0k |  | no | youprintin3d.de
52 | 12 | pcs | nut | M3 |  |  | no | youprintin3d.de
53 | 1 | pcs | nut, selflocking | M3 |  |  | no | youprintin3d.de
54 | 3 | pcs | knurl nuts | DIN 467 flat type stainless steel M3 | http://goo.gl/Mnz4qC | http://goo.gl/b58PFm | no | youprintin3d.de
55 | 2 | pcs | brass inserting nuts | M4 |  |  | no | aliexpress | 0.20 € |  | 0.20 €
56 | 100 | pcs | zip ties | 3x1x100 |  |  | no | ebay | 5.00 € |  | 7.00 €
57 | 1 | Set | cableguard | 12mm inner dia |  |  | no | ebay | 5.00 € |  | 5.00 €
 |  |  |  |  |  |  |  |  |  |  | 1095.41 €

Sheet: changelog
Changelog:
30.09.2017: | adjusted fasteners and rails for V3-update, deleted several old parts to accomodate the cohesion3d-mini board
01.07.2016: | changed amount of DC-DC-converter to 2
04.06.2016: | added 1 M3 nut, 1 M3 x 20mm, 2 M3 x 8mm, 2 M2x12mm and reduced 2 M3 x 6mm for mounting the Z-endstop and make it adjustable
02.06.2016: | updated spring dimensions
01.06.2016: | added 20cm short USB-cable to connect the raspberry Pi with the controllerboard
31.05.2016: | added link to 8 pol MPX connector
25.05.2016: | amount of M4x10 changed to 8
24.05.2016: | added 1 selflocking nut M3 (is used in the extruder)
24.05.2016: | changed "cheese-head screw torx M3 x 8mm" to 6mm, because Misumi Rails are 0,5mm flatter than Hiwin-ones
24.05.2016: | added raspberry Pi 3 + 32GB microSD to BOM
24.05.2016: | added changelog to BOM

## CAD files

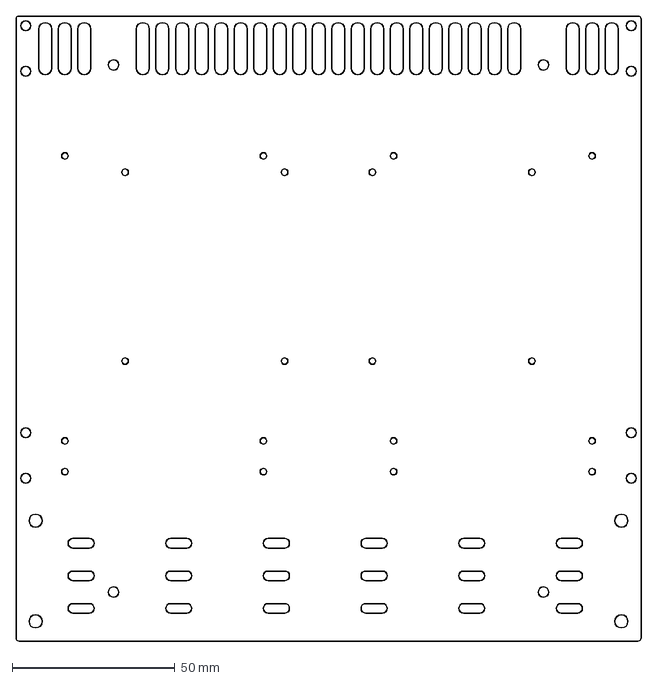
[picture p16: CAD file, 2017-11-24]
enclosure/2mm thick stainless steel/1. update/bodenplatte.DXF
192.0 x 192.0 mm

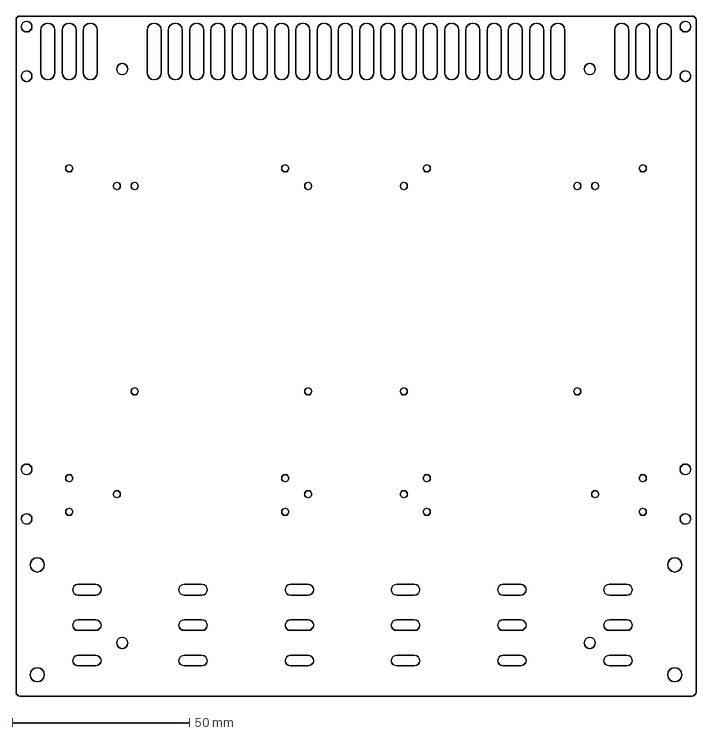
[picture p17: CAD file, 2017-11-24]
enclosure/2mm thick stainless steel/2. update/bodenplatte.DXF
192.0 x 192.0 mm

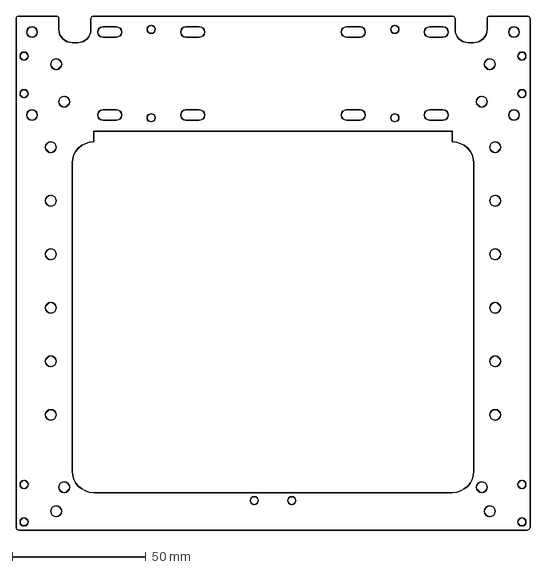
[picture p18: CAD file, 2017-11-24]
enclosure/2mm thick stainless steel/3. update/traegerplatte_A.DXF
192.0 x 192.0 mm

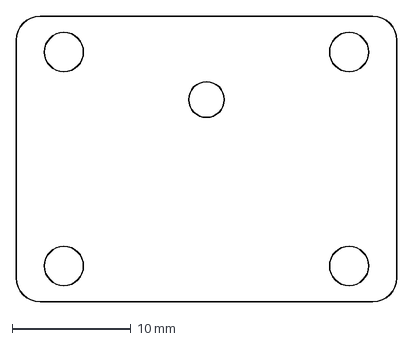
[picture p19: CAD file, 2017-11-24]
enclosure/2mm thick stainless steel/original/y_deckplatte_B.DXF
32.0 x 24.0 mm

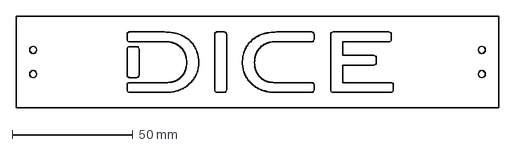
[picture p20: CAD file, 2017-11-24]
enclosure/4mm thick aluminium/1. update/front_DICE.DXF
200.0 x 38.0 mm

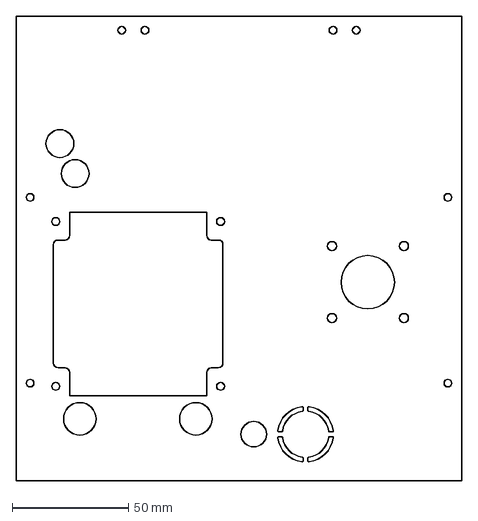
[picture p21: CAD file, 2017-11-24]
enclosure/4mm thick aluminium/2. update (watercooling)/rueckwand.DXF
192.0 x 200.0 mm

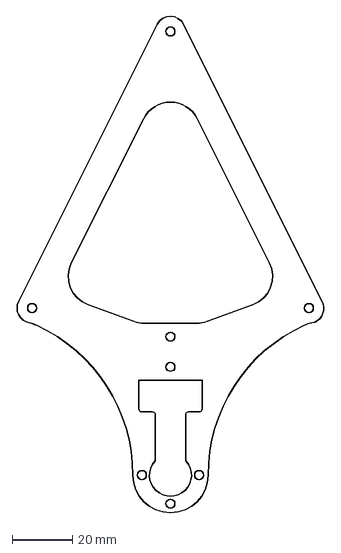
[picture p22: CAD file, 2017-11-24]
enclosure/4mm thick aluminium/3. update/traeger.DXF
102.4 x 165.0 mm

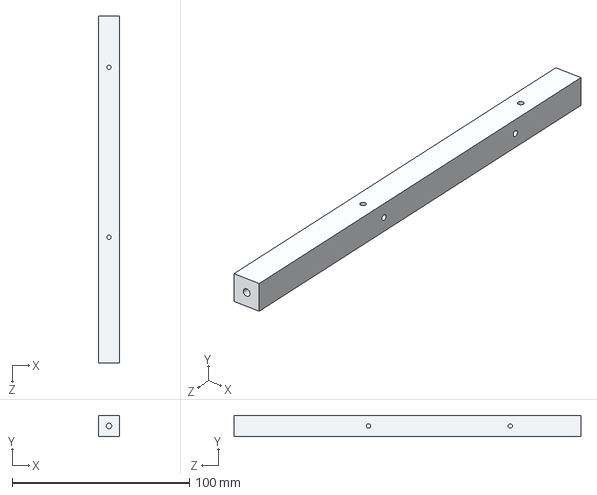
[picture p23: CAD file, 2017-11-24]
milled parts/pillar_B_12x12x196mm_2x.STEP
12.0 x 12.0 x 196.0 mm

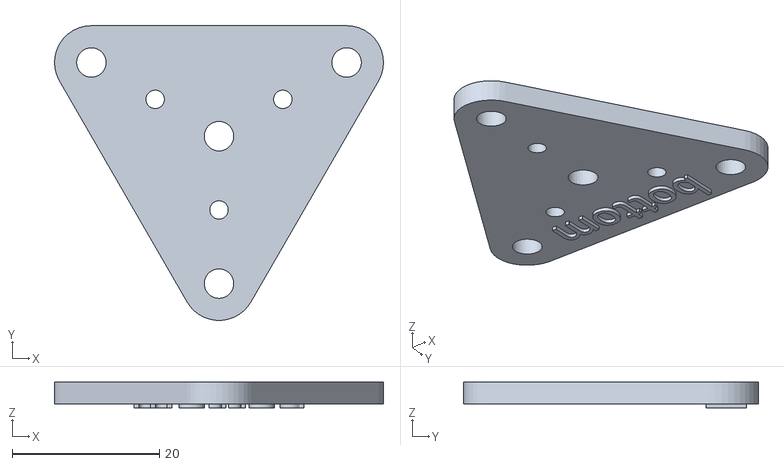
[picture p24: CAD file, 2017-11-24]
optional/casting form for bed feet/STL/bottom.STL
44.6 x 40.0 x 3.50

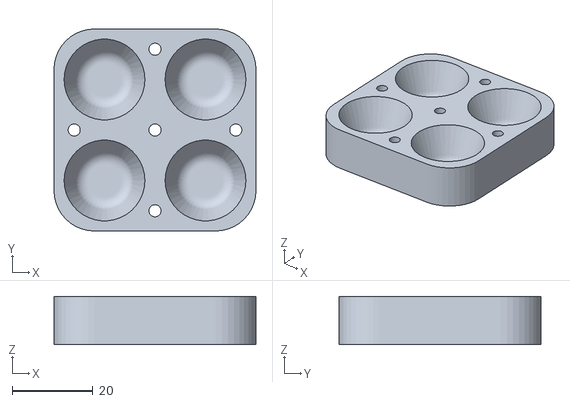
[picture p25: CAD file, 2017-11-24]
optional/casting_noise_dampening_silicon_rubber_feet/files/Unterteil.STL
50.0 x 50.0 x 12.0

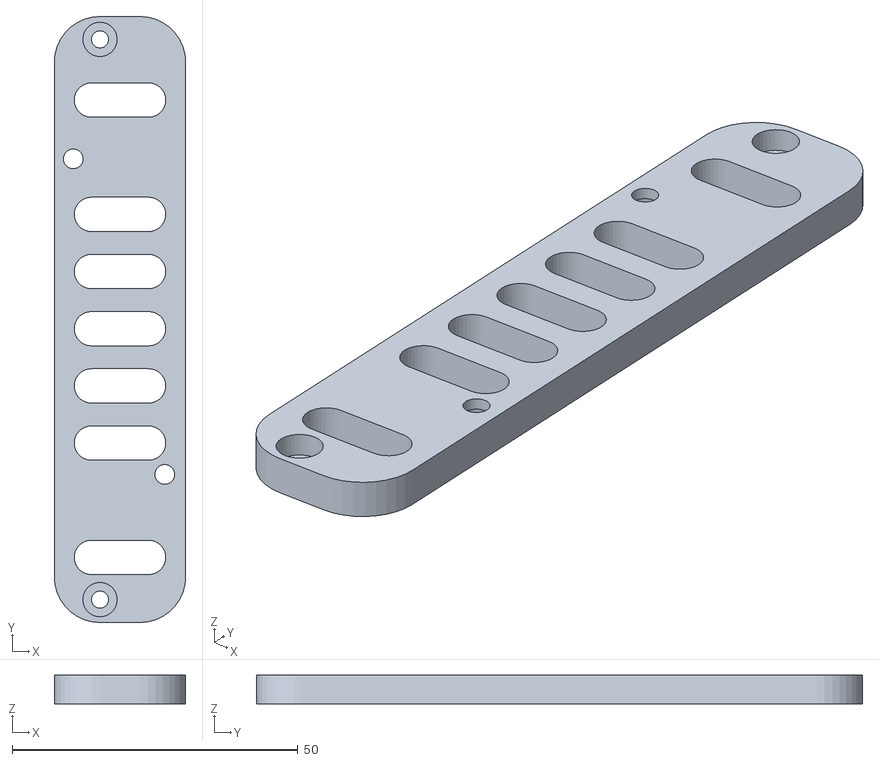
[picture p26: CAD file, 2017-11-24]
optional/PiUSV+/battery-mount.STL
23.0 x 106.0 x 5.00

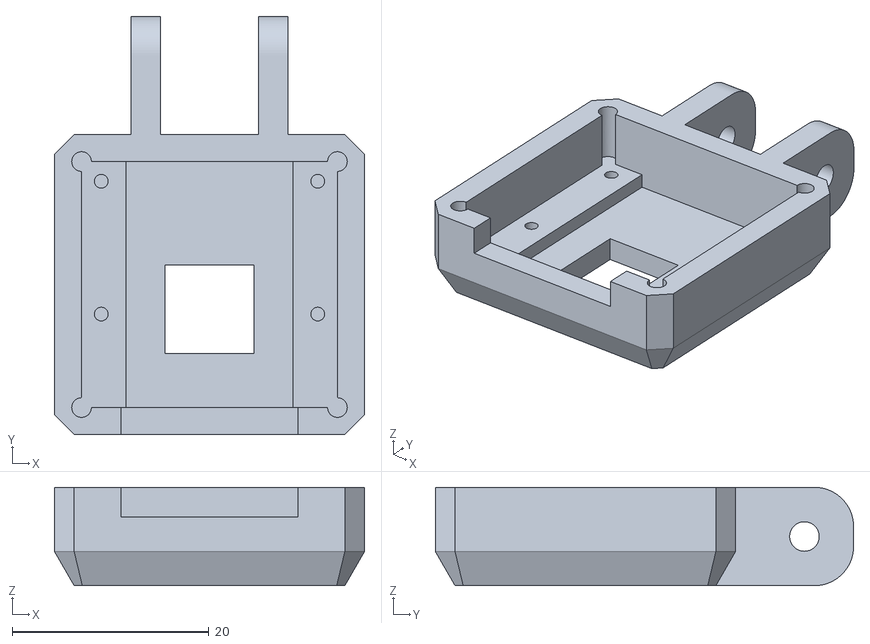
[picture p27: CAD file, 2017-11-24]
optional/raspberry pi camera case/camera_case.stl
31.5 x 42.5 x 10.0

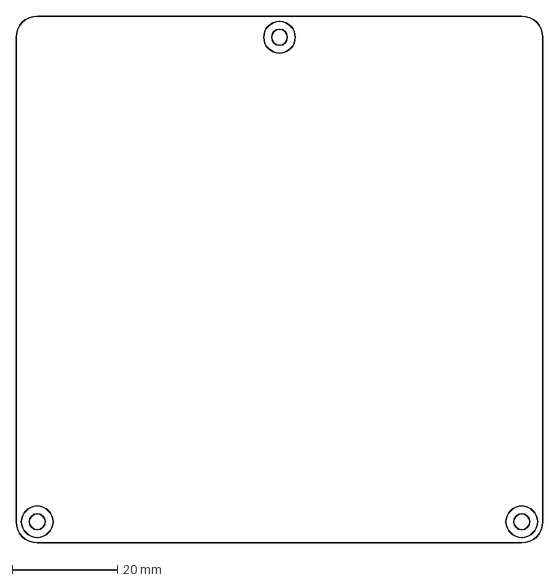
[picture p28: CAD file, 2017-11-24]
printbed/printbed_100x100.DXF
100.0 x 100.0 mm

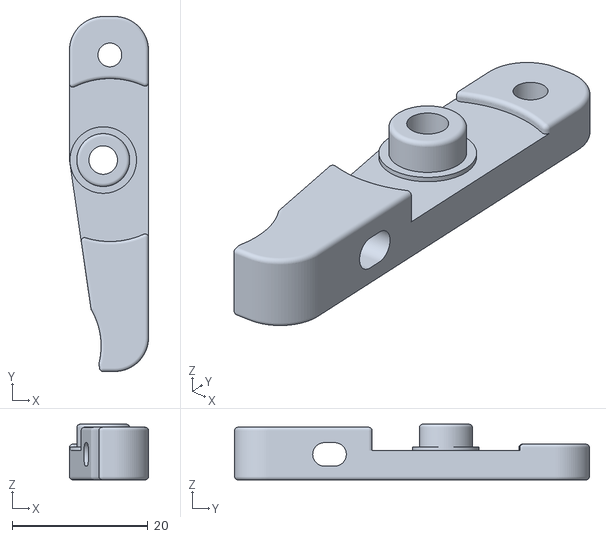
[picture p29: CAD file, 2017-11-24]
printed parts/Extruder/C_B_E_longer_idler_2.stl
11.7 x 52.3 x 8.20

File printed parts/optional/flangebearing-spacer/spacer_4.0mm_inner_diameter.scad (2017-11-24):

//
// DICE Schlauchstuecke
//
// Credit: reprap.org  Forum-user 'bastard'
//


//
// Schlauch 4x6mm
// Laenge 4x 4mm, 8x 13mm, 4x 22mm
//

$fn=30;
innendurchmesser=4;
aussendurchmesser=6;

stuecke=[ [4, 4], [8, 13], [4, 22] ];

for (stueck=stuecke)
{
	for(a= [1 : stueck[0]])
	{
		for(b=stueck[1])
		{
			translate([aussendurchmesser * a * 1.5, b, 0])
				schlauchstueck(b);
		}
	}
}

module schlauchstueck(hoehe)
{
	difference()
	{
		cylinder(d=aussendurchmesser, h=hoehe);
		
		translate([0,0,-1])
			cylinder(d=innendurchmesser, h=hoehe + 2);
	}
}

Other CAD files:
printed parts/optional/40mm fan holder/L+-fter_Halter_2.STL
printed parts/optional/anti-backlash clip for bowden pushfit/Bowden_Clip_v1-2.STL
printed parts/optional/flangebearing-spacer/Spacer_4.5mm_inner_diameter.stl
enclosure/2mm thick stainless steel/1. update/deckplatte.DXF
enclosure/2mm thick stainless steel/1. update/luefterhalter.DXF
enclosure/2mm thick stainless steel/1. update/traegerplatte_A.DXF
enclosure/2mm thick stainless steel/1. update/traegerplatte_B.DXF
enclosure/2mm thick stainless steel/1. update/x_platte_A.DXF
enclosure/2mm thick stainless steel/1. update/x_platte_B.DXF
enclosure/2mm thick stainless steel/1. update/y_deckplatte_A.DXF
enclosure/2mm thick stainless steel/1. update/y_grundplatte.DXF
enclosure/2mm thick stainless steel/1. update/z_achse.DXF
enclosure/2mm thick stainless steel/2. update/deckplatte.DXF
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

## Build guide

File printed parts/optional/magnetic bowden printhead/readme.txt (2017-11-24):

magnetic interchangeable printhead for the DICE

for short overview, see: https://youtu.be/_YarIbAeLJ0

Besides the 2 printed parts you will need 4 round magnets, 10mm diameter and 5mm thick.

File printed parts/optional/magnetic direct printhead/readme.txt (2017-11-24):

magnetic interchangeable direct-printhead for the DICE

For short overview, see the picture.

Besides the 2 printed parts you will need 4 round magnets, 10mm diameter and 5mm thick.
Extruder in the picture is an E3D-Titan and a coomon NEMA17-20mm long (like 17HS08-1004S for roughly 20€)

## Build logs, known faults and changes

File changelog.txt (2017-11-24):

Changelog:

25.09.2017:
- modified "enclosure/4mm thick aluminium/z_achse.DXF" for less post processing.

26.03.2017:
- #secondDICEupdate -> several updates at multiple different places. Biggest part: watercooling drivers and hotend.
   o modified enclosure-parts:
      ~ bodenplatte.DXF: added 2 bores to match cohesion3d-mini and several other bores for more features.
      ~ luefterhalter.DXF: redesigned the cutouts for more space inside the electronic compartment
      ~ traegerplatte_B.DXF: added an additional cutout to make the z-axis motor changeable without 
        tearing the whole DICE appart. (idea of Andre Reichert, Thanks!)
      ~ front_DICE.DXF: replaced a frontpart to one with DICE-logo
      ~ z_achse.DXF: removed the pillar in the middle to get more space inside the electronic compartment

   o added firmware and config for the board "cohesion3d-mini" at "firmware/cohesion3d-mini"
      ~ the reason for adding this board to the DICE is a very high failure rate of the AZSMZ-mini 
        and zero to none support from the creator of the AZSMZ-board. The Cohesion3d-Mini does only 
        support 4 stepper drivers but has more FETs for fans and stuff and should be of a higher
        quality. It also has better connectors (easier to install wires) and 24V and/or 5V outputs 
        that remove the need for the tiny stepdown-converters. The creator Ray Kholodovsky is an active 
        dev with a support-community on g+ and reacts quickly to nearly any question. 

   o added watercooling for the DICE. 
      ~ With this, the stepper drivers and the hotend are watercooled. This reduces the overall soundlevel,
        makes a much better cooling of the heatbreak, enables to mount 2 radial blower fans for more
        print-cooling and it does look cool, too ;)
         - changed backside: additional cutout for the radiator and repositioned the other bores. The 20mm bore 
           is now "closed" and can opened if needed.
         - changed right sidecover: It has a big cutout on the bottom to make room for the big heatsink of the 
           stepper drivers. I suggest using corrosion-resistant material such as stainless steel.
         - The heatsink for the stepperdrivers is put on the inside of the sidecover and a matching acrylic sheet
           on the outside. The acrylic part has 2 holes with G1/4" tap to mount hose-connectors like they are used
           at PC-watercooling systems.
         - added a watercooled printhead. The printhead consists of 3 parts. The actual heatsink is made of an 
           acrylic cover and a matching cooling block. Then the mount for the heatbreak gets scewed to the 
           cooling block and is designed in a very simple rectangular block. This way, each on is able to easily 
           adapt other mounts for different heatbreaks. Just the heatsink on any flat surface to cool it.
         - The watercooled printhead is mounted with 4 screws to the x-carriage with a solid 5mm thick aluminium 
           plate. Loosening these 4 screws frees the printhead for maintenance.
         - Watercooling the printhead allows for a much smaller design. This way, there is now room for a second 
           partcooling fan. Additionally, there are new covers for the fans with an integrated fanshrout and cable-mount.
         - On top of the DICE, a pump and reservoir needs to be installed. I highly recommend the alphacooling DC-LT
           pump with matching reservoir for ~50€. The pump-housing has matching mounting points to the DICE. You can
           easily mount the pump with vibration dampers to reduce noice even further.
         - The acrylic transparent covers allow for tinted water to match the color of your printed parts.

02.02.2017:
- added preconfigured Raspberry Pi Image "OctoPi 0.13" with all the needed additions for using the PiUPS
   o the image file can be found in "DICE/optional/PiUSV+/"

28.01.2017:
- modified "enclosure/4mm thick aluminium/z_achse.DXF" to make it possible to rout wires for lighting.

08.01.2017:
- fixed changelog.txt wordwrap in file (line endings got played with)
- added another magnetic printhead: a direct-extruder
   o files as .STL, .STEP and Solidworks are located in printed parts -> optional -> magnetic direct printhead 
     including a timelaps and picture of the assembly
- added „front_DICE.dxf“ to enclosure -> 4mm thick aluminium

31.12.2016:
- added folder "Simplify3D"
   o added some .fff demo-files

18.12.2016:
- added first Addon for the DICE: magnetic interchangeable printhead
   o files as .STL, .STEP and Solidworks-Assembly are located in printed parts -> optional -> magnetic printhead  

28.11.2016:
- changed the recommended bowden tube clip to a better one
   o http://www.thingiverse.com/thing:936611 bowden tube clip by walter

15.11.2016:
- modified the feedrates in the example-config file.
   o Smoothie won't do more than 49980 mm/min at 16µStepping. Adjusted for that.

09.11.2016:
- added STL file "printed parts/z-endstop-mount-9.5mm(omron)"
   o this part has a 9.5mm distance between the two holes for screwing in the microswitch. 
     This is needed for bigger switches like some sort of the Omron-ones.

15.08.2016:
- added STL file "printed parts/optional/x_carriage_fanholder_for_SKT_hotend/x_carriage_fanholder_for_SKT_hotend.stl"
   o this part is needed, if you are going to mount the somewhat different hotend from SKT

25.06.2016:
- added folder "CAD"
   o added file "CAD/DICE.zip" which contains the complete CAD-Files for Solidworks
   o added file "CAD/DICE.STEP" which contains the complete CAD-modell in STEP-format

19.06.2016:
- minor change to DICE/enclosure/2mm thick stainless steel/deckplatte.dxf
   o reduced the width of the sheet by 1mm to get a better fit and not to scratch the enclosure anylonger, when dismounting the sheet for maintenence.

05.06.2016:
- update of model z-endstop-mount.STL for easier print and better fit

02.06.2016:
- added optional/casting form for bed feet
  o 3 STL files
  o 4 drawings, including parts list

01.06.2016:
- added folder „drawings“
  o added 2 drawings

31.05.2016:
- added printed part: z-endstop-mount.stl
  o for mounting the z—max-endstop
- added optional/raspberry pi camera case
  o case and joint for the raspicam

29.05.2016:
- added logo „DICE“ to printed part „x_carriage_fan_holder_1x.stl“

28.05.2016:
- added /optional/PiUSV+
  o added files and datasheets for using PiUSV+
- added /optional/casting_noise_dampening_silicon_rubber_feet
  o Mold to cast noise-dampening silicon feet for the DICE

24.05.2016:
- added changelog.txt
- minor updates in BOM (see changelog-tab in BOM)
- added anti-backlash clip for bowden-pushfit

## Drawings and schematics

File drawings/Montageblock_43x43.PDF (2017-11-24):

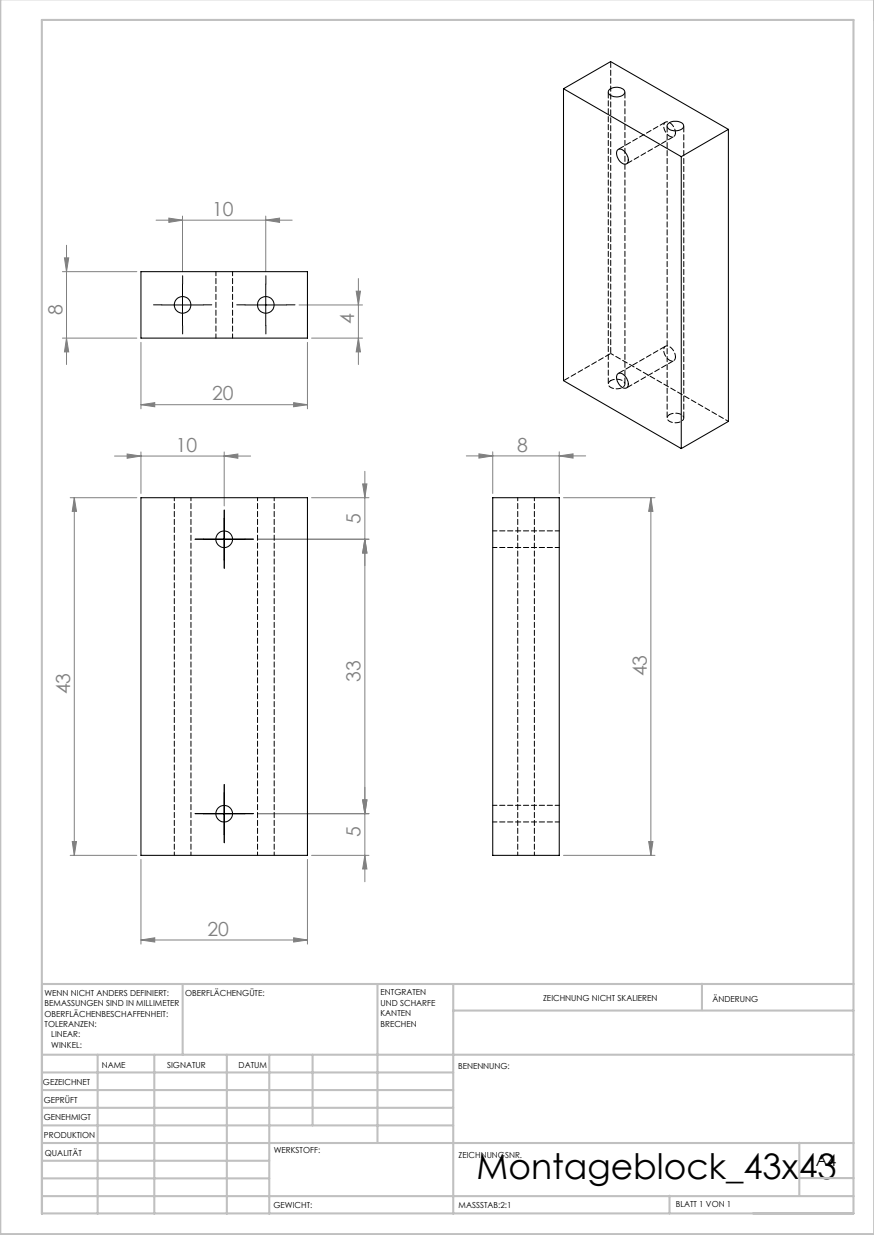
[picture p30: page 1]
MASSSTAB:2:1; BLATT 1 VON 1; ZEICHNUNG NICHT SKALIEREN; ÄNDERUNG; UND SCHARFE; WENN NICHT ANDERS DEFINIERT:; OBERFLÄCHENGÜTE:

BEMASSUNGEN SIND IN MILLIMETER
OBERFLÄCHENBESCHAFFENHEIT:
TOLERANZEN:
LINEAR:
WINKEL:

NAME | SIGNATUR | DATUM | | | | BENENNUNG:
QUALITÄT | | | | WERKSTOFF: | Montageblock_43x43 GEWICHT: ZEICHNUNGSNR. | A4

GEZEICHNET
GEPRÜFT
GENEHMIGT
PRODUKTION

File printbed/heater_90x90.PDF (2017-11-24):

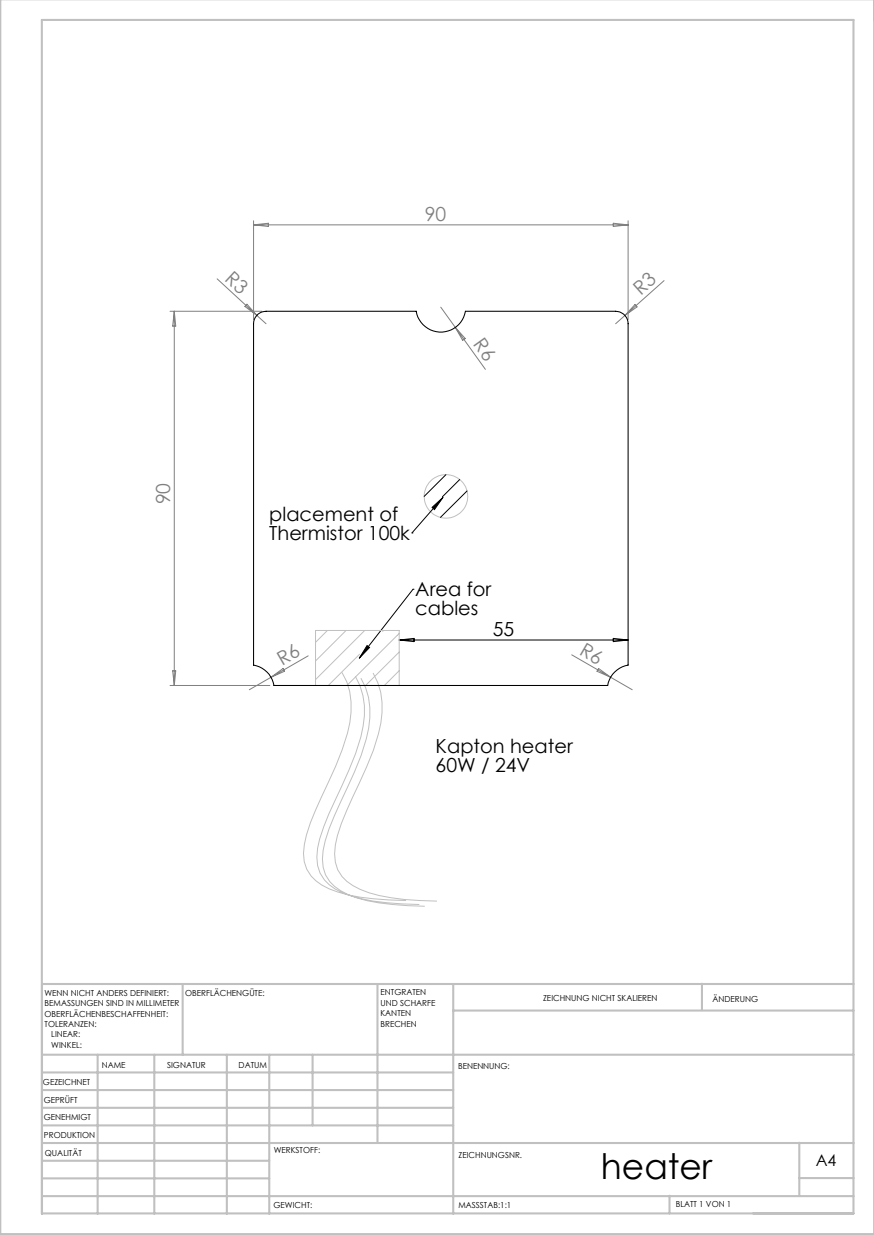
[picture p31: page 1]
Area for; placement of Thermistor 100k; Kapton heater 60W / 24V; MASSSTAB:1:1; BLATT 1 VON 1; ZEICHNUNG NICHT SKALIEREN; ÄNDERUNG; UND SCHARFE; WENN NICHT ANDERS DEFINIERT:; OBERFLÄCHENGÜTE:

BEMASSUNGEN SIND IN MILLIMETER
OBERFLÄCHENBESCHAFFENHEIT:
TOLERANZEN:
LINEAR:
WINKEL:

NAME | SIGNATUR | DATUM | | | | BENENNUNG:

GEZEICHNET
GEPRÜFT
GENEHMIGT
PRODUKTION
QUALITÄT | | | | WERKSTOFF: | heater GEWICHT: ZEICHNUNGSNR. | A4

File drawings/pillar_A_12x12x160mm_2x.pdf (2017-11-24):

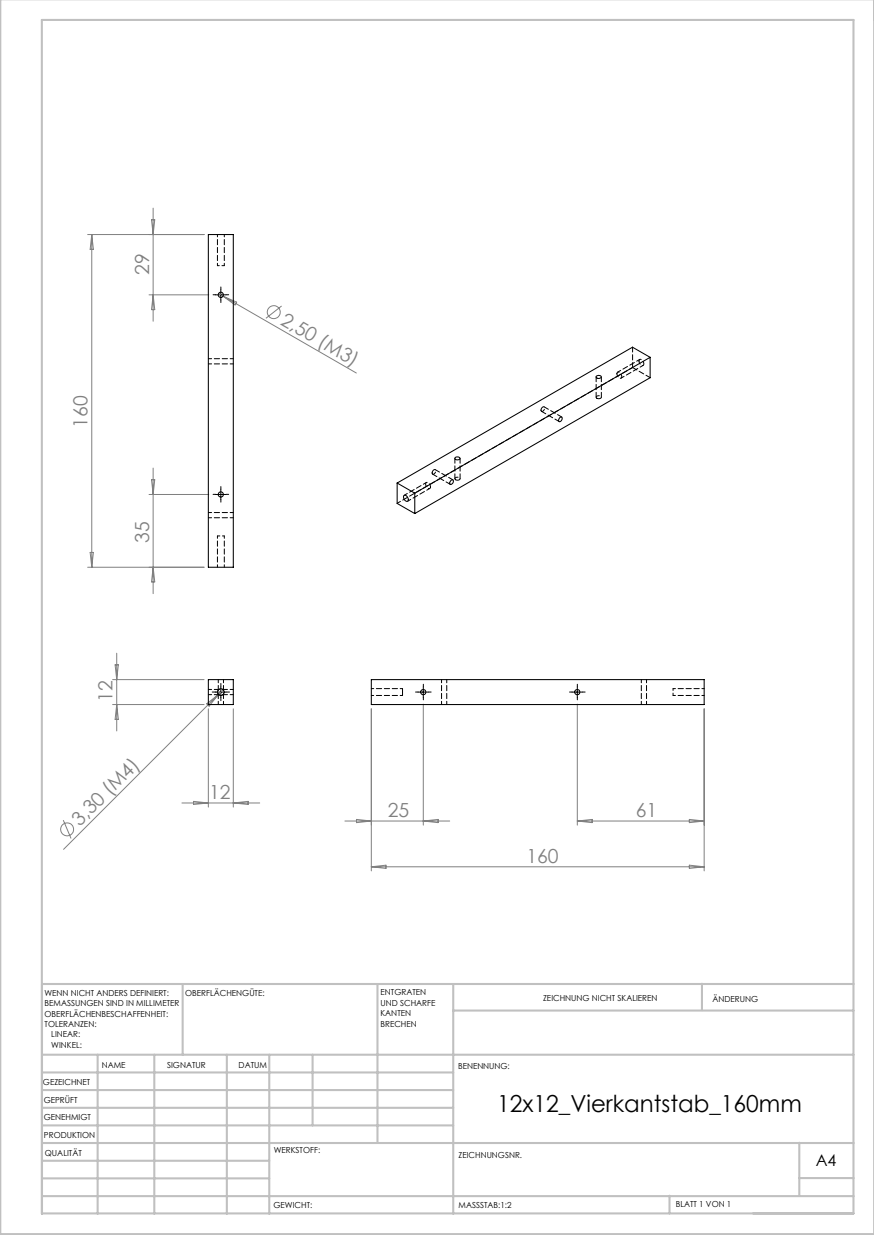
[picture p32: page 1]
MASSSTAB:1:2; BLATT 1 VON 1; ZEICHNUNG NICHT SKALIEREN; ÄNDERUNG; UND SCHARFE; WENN NICHT ANDERS DEFINIERT:; OBERFLÄCHENGÜTE:

BEMASSUNGEN SIND IN MILLIMETER
OBERFLÄCHENBESCHAFFENHEIT:
TOLERANZEN:
LINEAR:
WINKEL:

NAME | SIGNATUR | DATUM | | | | BENENNUNG: 12x12_Vierkantstab_160mm

GEZEICHNET
GEPRÜFT
GENEHMIGT
PRODUKTION
QUALITÄT | | | | WERKSTOFF: | ZEICHNUNGSNR. | A4

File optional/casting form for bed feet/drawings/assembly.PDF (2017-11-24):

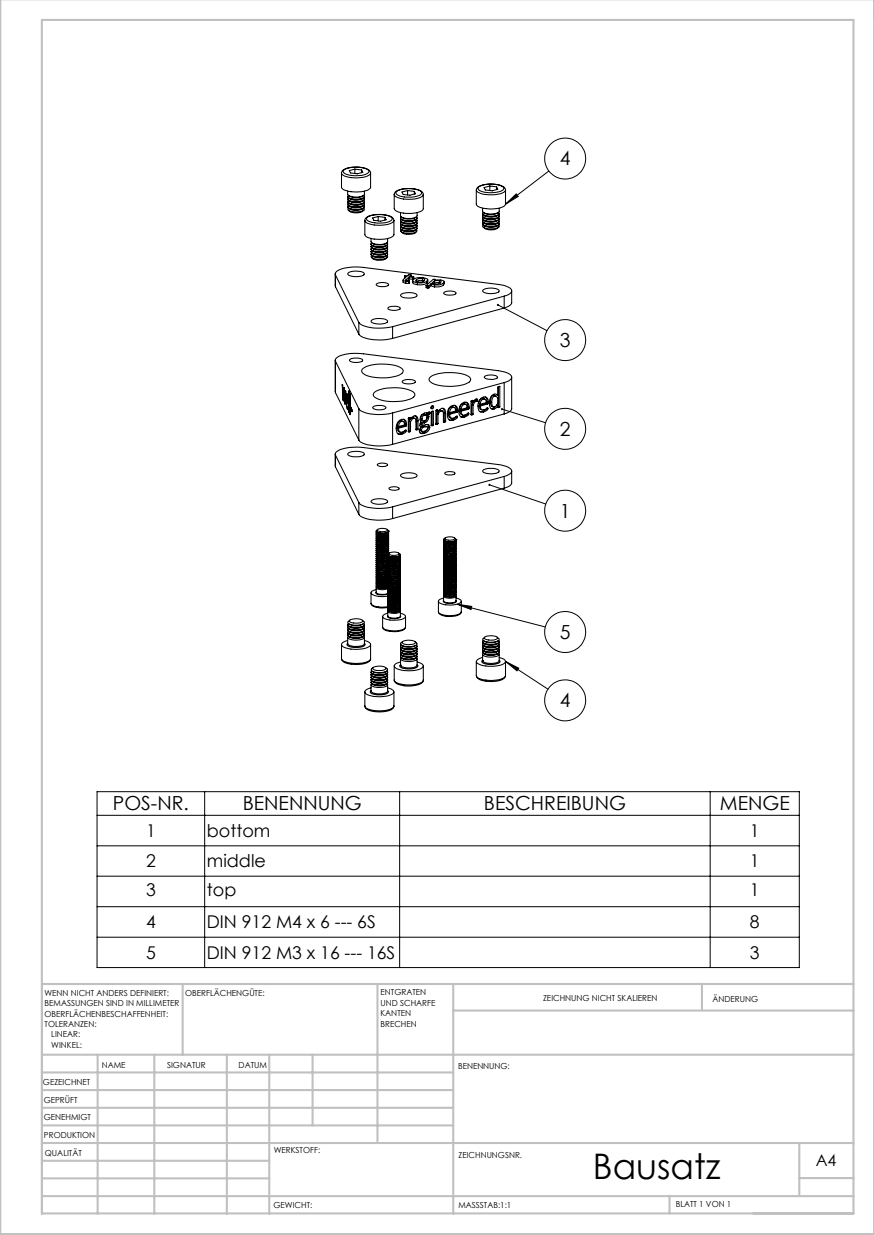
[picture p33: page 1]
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

POS-NR. | BENENNUNG | BESCHREIBUNG | MENGE
1 | bottom | | 1
2 | middle | | 1
3 | top | | 1
4 | DIN 912 M4 x 6 --- 6S | | 8
5 | DIN 912 M3 x 16 --- 16S | | 3

BEMASSUNGEN SIND IN MILLIMETER
OBERFLÄCHENBESCHAFFENHEIT:
TOLERANZEN:
LINEAR:
WINKEL:

NAME | SIGNATUR | DATUM | | | | BENENNUNG:

GEZEICHNET
GEPRÜFT
GENEHMIGT
PRODUKTION
QUALITÄT | | | | WERKSTOFF: | Bausatz GEWICHT: ZEICHNUNGSNR. | A4

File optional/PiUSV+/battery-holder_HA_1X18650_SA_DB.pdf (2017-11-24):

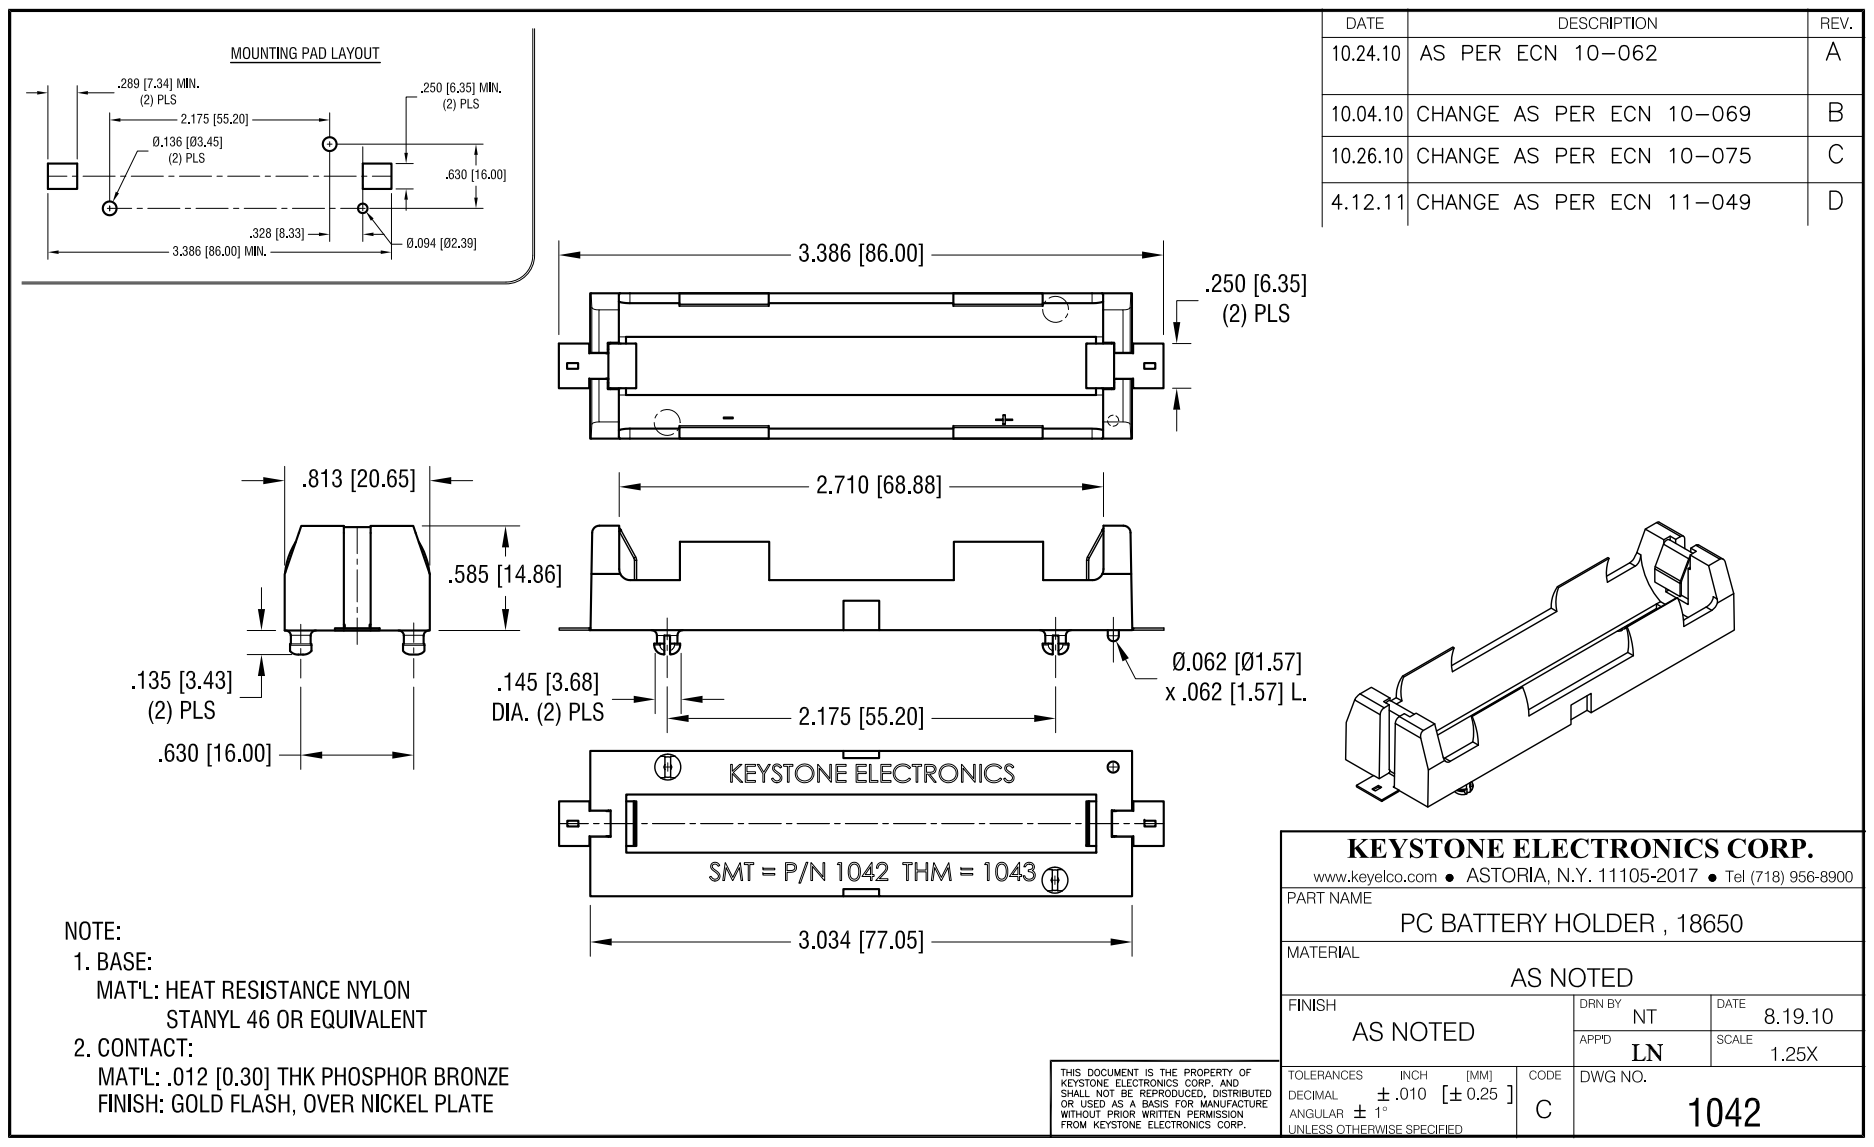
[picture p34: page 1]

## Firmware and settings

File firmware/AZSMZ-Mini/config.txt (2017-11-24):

#######################################
###									###
###			GENERAL INFO			###
###									###
#######################################

# Config: As of 15th may 2016: config.txt verified.
# Firmware is Smoothieware.
# Provided config-file is for the AZSMZ-mini V2.1 and to use in the 3D-printer ‚DICE’.
# More information at www.well-engineered.net

# there are advanced options to configure a pin:
# 	!	invert pin
# 	o	set pin to open drain
# 	^	set pin to pull up
# 	v	set pin to pull down
# 	-	to set no pullup
# 	@	to set repeater mode

# EXAMPLE:
# set_example_pin	1.23!^ 
# will set the pin to inverted pull up


#######################################
###									###
###			GENERAL MOTION 			###
###									###
#######################################

	#=================#
	# MOTION-SETTINGS #
	#=================#

arm_solution				corexy	 	# Sets the arm solution for this machine. The arm solution converts position in millimetres into actuator positions ( usually in steps ). On cartesian machines those are proportional to each other, but for example on a linear delta machine, some fancy math is required for the conversion. Possible values : cartesian, corexy, linear_delta, rotatable_cartesian, morgan

alpha_steps_per_mm			80			# Steps per millimetre for alpha stepper motor ( this is the X axis for a cartesian machine )
beta_steps_per_mm			80			# Steps per millimetre for beta stepper motor ( this is the Y axis for a cartesian machine )
gamma_steps_per_mm			800			# Steps per millimetre for gamma stepper motor ( this is the Z axis for a cartesian machine )

acceleration					8000	# Acceleration in millimetres/second/second. Higher values make your machine faster and shakier, lower values make your machine slower and sturdier. This is generally proportional to the weight of the tool you are trying to move.
z_acceleration					2000	# Acceleration for Z only moves, same as acceleration but for movements of the Z axis. Do not set this value if you use a delta arm solution.
acceleration_ticks_per_second	1000	# Number of times per second the speed is updated. Do not modify unless you know exactly what you are doing !

junction_deviation			0.3			# Similar to the old "max_jerk", in millimeters. Defines how much the machine slows down when decelerating proportional to the vector angle of change of direction. See here and here. Lower values mean being more careful, higher values means being faster and have more jerk
z_junction_deviation		0			# Junction deviation for Z only moves, -1 uses junction_deviation, 0 disables junction_deviation on z moves. Do not set this value if you use a delta arm solution.

	#================#
	# SPEED SETTINGS #
	#================#

default_feed_rate			30000		# Default rate for G1/G2/G3 moves in millimetres/minute. This is overrided by the first F ( feedrate ) parameter after reset, and never used again.
default_seek_rate			30000		# Default rate for G0 moves in millimetres/minute

x_axis_max_speed			49980		# Maximum allowable speed for the X axis, in millimetres/minute. Smoothie will never exceed that value for that axis.
y_axis_max_speed			49980		# Maximum allowable speed for the Y axis, in millimetres/minute. Smoothie will never exceed that value for that axis.
z_axis_max_speed			1800		# Maximum allowable speed for the Z axis, in millimetres/minute. Smoothie will never exceed that value for that axis.

alpha_max_rate				120000		# Maximum allowable speed for this actuator ( as opposed to axis, they are the same on a cartesian machine, but not on a delta machine for example ), in millimetres/minute.
beta_max_rate				120000		# Maximum allowable speed for this actuator, in millimetres/minute.
gamma_max_rate				1800		# Maximum allowable speed for this actuator, in millimetres/minute.

	#==================#
	# SPECIAL SETTINGS #
	#==================#

mm_per_arc_segment			0.5			# Arcs are cut into segments ( lines ), this is the length for those segments. Smaller values mean more resolution, higher values mean faster computation
planner_queue_size			32			# Defines how many blocks ( line segments ) are stored in RAM for look-ahead acceleration calculation. Do not change this unless you know exactly what you are doing !
minimum_planner_speed		20			# Sets the minimum planner speed in millimetres/sec. This is the lowest speed the planner will ever set a move to. Not generally useful.
microseconds_per_step_pulse	1			# Duration of step pulses to the stepper motor drivers, in microseconds
base_stepping_frequency		100000		# Base frequency for stepping, higher values gives smoother movement. Do not modify unless you know exactly what you are doing, 100khz is the only officially supported value.


#######################################
###									###
###			STEPPER MOTORS 			###
###									###
#######################################

	#=================#
	# Slot 1 - empty  #
	#=================#

## step_pin		2.0		# Pin for stepper step signal
## dir_pin		0.5!	# Pin for stepper direction
## en_pin		0.4		# Pin for enable pin


	#=================#
	# Slot 2 - X-AXIS #
	#=================#

alpha_step_pin		2.1		# Pin for alpha stepper step signal
alpha_dir_pin		0.11!	# Pin for alpha stepper direction
alpha_en_pin		0.10	# Pin for alpha enable pin
#alpha_current		1.0		# M1 stepper motor driver current, in Amperes.

	#=================#
	# Slot 3 - Y-AXIS #
	#=================#

beta_step_pin		2.2		# Pin for beta stepper step signal
beta_dir_pin		0.20!	# Pin for beta stepper direction
beta_en_pin			0.19	# Pin for beta enable
#beta_current		1.0		# M2 stepper motor driver current, in Amperes.

	#=================#
	# Slot 4 - Z-AXIS #
	#=================#

gamma_step_pin		2.3		# Pin for gamma stepper step signal
gamma_dir_pin		0.22!	# Pin for gamma stepper direction
gamma_en_pin		0.21	# Pin for gamma enable
#gamma_current		1.0		# M3 stepper motor driver current, in Amperes.


	#===================#
	# Slot 5 - Extruder #
	#===================#

extruder.hotend_1.step_pin		2.8		# Pin for extruder stepper motor driver's step signal
extruder.hotend_1.dir_pin		2.13!	# Pin for extruder stepper motor driver's direction signal
extruder.hotend_1.en_pin		4.29	# Pin for extruder stepper motor driver's enable signal


###################################
###								###
###			EXTRUDER 			###
###								###
###################################

	#==========#
	# HOTEND 1 #
	#==========#

extruder.hotend_1.enable				true	# Whether to activate the extruder module at all. All configuration is ignored if false. Each time an extruder.module_name.enable line is encountered, an extruder module with the name «module_name» will be created.

extruder.hotend_1.steps_per_mm			145		# Steps/millimetre for the extruder stepper motor. This is the number of steps to move one millimetre of filament. Learn more
#extruder.hotend_1.filament_diameter	1.70	# Filament diameter, in millimetres, used for volumetric extrusion control.
extruder.hotend_1.default_feed_rate		1200	# Default rate in millimetres/minute for moves where only the extruder moves. This is only used if you have never provided a feedrate via the F parameter. Once you specify a F parameter, it will be used as the Extruder feed rate until you reset the board.
extruder.hotend_1.acceleration			500		# Acceleration for the extruder stepper motor, in millimetres/second/second
extruder.hotend_1.max_speed				100		# Maximum allowable speed for the extruder stepper motor, in millimetres/second

extruder.hotend_1.x_offset				0		# Extruder offset from origin in millimetres for the X axis. This is useful when you have multiple extruders to specify the offset from each extruder to the first one.
extruder.hotend_1.y_offset				0		# Extruder offset from origin in millimetres for the Y axis.
extruder.hotend_1.z_offset				0		# Extruder offset from origin in millimetres for the Z axis.

extruder.hotend_1.retract_length			2		# Retract length in millimetres. Retract is a retractation of the filament called using the G10 G-code. It is recovered ( reverted ) using the G11 G-code. Learn more about retractation
extruder.hotend_1.retract_feedrate			60		# Retract feed-rate ( filament speed ) in millimetres/second
extruder.hotend_1.retract_recover_length	0		# Additional length when recovering ( if you retract by 1mm, you will be recovering by 1mm plus this value )
extruder.hotend_1.retract_recover_feedrate	8		# Recovery feed-rate in millimetres/second (should be less than retract feedrate)
extruder.hotend_1.retract_zlift_length		0		# Z-lift on retract in millimeters, set to 0 if you want to disable retraction Z-lift. Z-lift is a small increase in the Z axis position when retracting.
extruder.hotend_1.retract_zlift_feedrate	1800	# Z-lift feed-rate in millimetres/minute ( Note : mm/min NOT mm/sec)


###############################################
###											###
###			TEMPERATURE CONTROL 			###
###											###
###############################################

	#==========#
	# HOTEND 1 #
	#==========#
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

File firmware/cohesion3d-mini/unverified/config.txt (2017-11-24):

# Smoothieboard configuration file, see http://smoothieware.org/configuring-smoothie
# NOTE Lines must not exceed 132 characters, and '#' characters mean what follows is ignored
## Robot module configurations : general handling of movement G-codes and slicing into moves

# Basic motion configuration
default_feed_rate                            30000             # Default speed (mm/minute) for G1/G2/G3 moves
default_seek_rate                            30000             # Default speed (mm/minute) for G0 moves
mm_per_arc_segment                           0.0              # Fixed length for line segments that divide arcs, 0 to disable
#mm_per_line_segment                         5                # Cut lines into segments this size
mm_max_arc_error                             0.01             # The maximum error for line segments that divide arcs 0 to disable
                                                              # note it is invalid for both the above be 0
                                                              # if both are used, will use largest segment length based on radius

# Arm solution configuration : Cartesian robot. Translates mm positions into stepper positions
# See http://smoothieware.org/stepper-motors
arm_solution                                 corexy
alpha_steps_per_mm                           80               # Steps per mm for alpha ( X ) stepper
beta_steps_per_mm                            80               # Steps per mm for beta ( Y ) stepper
gamma_steps_per_mm                           400             # Steps per mm for gamma ( Z ) stepper

# Planner module configuration : Look-ahead and acceleration configuration
# See http://smoothieware.org/motion-control
acceleration                                 3000             # Acceleration in mm/second/second.
z_acceleration                              1000              # Acceleration for Z only moves in mm/s^2, 0 uses acceleration which is the default. DO NOT SET ON A DELTA
junction_deviation                           0.05             # See http://smoothieware.org/motion-control#junction-deviation
z_junction_deviation                        0.0              # For Z only moves, -1 uses junction_deviation, zero disables junction_deviation on z moves DO NOT SET ON A DELTA

# Cartesian axis speed limits
x_axis_max_speed                             30000            # Maximum speed in mm/min
y_axis_max_speed                             30000            # Maximum speed in mm/min
z_axis_max_speed                             600              # Maximum speed in mm/min

# Stepper module configuration 
# Pins are defined as  ports, and pin numbers, appending "!" to the number will invert a pin
# See http://smoothieware.org/pin-configuration and http://smoothieware.org/pinout
alpha_step_pin                               2.0              # Pin for alpha stepper step signal
alpha_dir_pin                                0.5              # Pin for alpha stepper direction, add '!' to reverse direction
alpha_en_pin                                 0.4              # Pin for alpha enable pin
alpha_current                                1.5              # X stepper motor current
alpha_max_rate                               30000.0          # Maximum rate in mm/min

beta_step_pin                                2.1              # Pin for beta stepper step signal
beta_dir_pin                                 0.11             # Pin for beta stepper direction, add '!' to reverse direction
beta_en_pin                                  0.10             # Pin for beta enable
beta_current                                 1.5              # Y stepper motor current
beta_max_rate                                30000.0          # Maxmimum rate in mm/min

gamma_step_pin                               2.2              # Pin for gamma stepper step signal
gamma_dir_pin                                0.20             # Pin for gamma stepper direction, add '!' to reverse direction
gamma_en_pin                                 0.19             # Pin for gamma enable
gamma_current                                1.5              # Z stepper motor current
gamma_max_rate                               300.0            # Maximum rate in mm/min

## Extruder module configuration
# See http://smoothieware.org/extruder
extruder.hotend.enable                          true          # Whether to activate the extruder module at all. All configuration is ignored if false
extruder.hotend.steps_per_mm                    418.5           # Steps per mm for extruder stepper
extruder.hotend.default_feed_rate               1200           # Default rate ( mm/minute ) for moves where only the extruder moves
extruder.hotend.acceleration                    500           # Acceleration for the stepper motor mm/sec²
extruder.hotend.max_speed                       100            # Maximum speed in mm/s

extruder.hotend.step_pin                        2.3           # Pin for extruder step signal
extruder.hotend.dir_pin                         0.22          # Pin for extruder dir signal ( add '!' to reverse direction )
extruder.hotend.en_pin                          0.21          # Pin for extruder enable signal

# Extruder offset
#extruder.hotend.x_offset                        0            # X offset from origin in mm
#extruder.hotend.y_offset                        0            # Y offset from origin in mm
#extruder.hotend.z_offset                        0            # Z offset from origin in mm

# Firmware retract settings when using G10/G11, these are the defaults if not defined, must be defined for each extruder if not using the defaults
#extruder.hotend.retract_length                  3            # Retract length in mm
#extruder.hotend.retract_feedrate                45           # Retract feedrate in mm/sec
#extruder.hotend.retract_recover_length          0            # Additional length for recover
#extruder.hotend.retract_recover_feedrate        8            # Recover feedrate in mm/sec (should be less than retract feedrate)
#extruder.hotend.retract_zlift_length            0            # Z-lift on retract in mm, 0 disables
#extruder.hotend.retract_zlift_feedrate          6000         # Z-lift feedrate in mm/min (Note mm/min NOT mm/sec)

delta_current                                    1.5          # First extruder stepper motor current

# Second extruder module configuration
#extruder.hotend2.enable                         true         # Whether to activate the extruder module at all. All configuration is ignored if false
#extruder.hotend2.steps_per_mm                   140          # Steps per mm for extruder stepper
#extruder.hotend2.default_feed_rate              600          # Default rate ( mm/minute ) for moves where only the extruder moves
#extruder.hotend2.acceleration                   500          # Acceleration for the stepper motor, as of 0.6, arbitrary ratio
#extruder.hotend2.max_speed                      50           # mm/s

#extruder.hotend2.step_pin                       2.8          # Pin for extruder step signal
#extruder.hotend2.dir_pin                        2.13         # Pin for extruder dir signal ( add '!' to reverse direction )
#extruder.hotend2.en_pin                         4.29         # Pin for extruder enable signal

#extruder.hotend2.x_offset                       0            # x offset from origin in mm
#extruder.hotend2.y_offset                       25.0         # y offset from origin in mm
#extruder.hotend2.z_offset                       0            # z offset from origin in mm

#epsilon_current                                 1.5          # Second extruder stepper motor current
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
